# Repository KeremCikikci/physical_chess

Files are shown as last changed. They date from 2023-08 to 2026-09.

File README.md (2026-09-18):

# Physical Chess

https://github.com/KeremCikikci/physical_chess/assets/98697826/390d2253-afeb-4dcd-b02d-cf1ae9b18a00

# Working Principle

The trained artificial intelligence model recognizes the plus-shaped symbols on the game board 
through the camera mounted above the board. The adjacent corners of the symbols define the 
boundaries of the chessboard. As the symbols are detected with an artificial intelligence 
model, the position or angle of the camera can change while still determining the board.

Each frame captured by the camera undergoes various processes to eliminate proportional 
distortions and noise. In the obtained output, each frame is observed individually and 
converted from BGR format to HSV format. 

To reduce errors, colors of chess pieces that are far apart in the spectrum are made more 
distinguishable through different processes. Thus, the colors of the pieces on all squares are 
recorded. Since the positions of the pieces are known at the beginning of a chess game, there 
is no need to determine the types of pieces from the captured image.

For a chess game played on an online platform like Lichess, a unique ID is assigned to the 
game, and necessary information is retrieved using the Lichess API. However, to prevent 
cheating attempts, the Lichess API provides move information with a delay. Therefore, in a 
Lichess game, when a change occurs, a screenshot is taken to detect the move. Moves are 
recorded in the UCI (Universal Chess Interface) notation, which specifies the starting and 
ending coordinates of the pieces.

Additionally, the pieces obtained from Lichess at the beginning of the game are compared with 
the pieces detected in the squares from the camera. If they are not in sync, differing square 
coordinates are marked. When it's a player's turn, data flow is monitored from the Arduino, and 
if the button is pressed, the camera observes the pieces in the squares again. By identifying 
the differing pieces from the previously saved content, it's determined whether any piece has 
been captured. Then, a move notation is created in UCI format, and the move's validity is 
checked. The move is sent to the Lichess game with the assigned ID using the Lichess API. 
Additionally, time information obtained from the API is sent to Arduino via the Serial port.

At the start of each game, motors rotate until switches are triggered, bringing the robot arm 
to its home position. This resets all angle values and motors, enabling the robot arm to move 
to the desired coordinate in subsequent commands. After the home position, the arm moves to a 
waiting position. A function written in the Arduino code determines the slowest and fastest 
motor values on the arm, as well as the instantaneous speed during the motor's duty cycle, 
using a mathematical function.

While power is transmitted via a pulley on the X-axis, reducers are used on the Y and Z axes to 
greatly reduce the motor's speed and increase its torque by about 60 times. These reducers 
allow smooth movement of the load motors without excessive force.

In the final arm segment of the robot, there is a structure that lifts the chess pieces using a 
funnel. When triggered in the center of the funnel, a coil creates a magnetic field to lift the 
pieces by attracting the screws on top of them. Due to the high current drawn by the coil, it's 
triggered by a relay.

In the program, the chessboard is considered a coordinate axis, and after providing the 
coordinates where only the farthest point of the arm will be, the most economical angle values 
for the arm to reach the desired location are calculated. Motors bring the robot to the 
calculated angle values.

The movement path of the arm is determined by the move notation sent from the Serial monitor. 
When the arm movement is complete, it notifies the Python program. Additionally, time 
information is conveyed throughout the game. The remaining time of the opponents is visualised 
on displays. While each LED control of the displays requires 20 separate data wires, with 2 shift 
register chips, the data is transmitted using only 3 wires. The shift registers sequentially 
light up the required LEDs in each segment of the display. This process happens so quickly that 
the human eye perceives the LEDs as lit simultaneously.

# Complete Documentation
[RoboChess_ Digitalisierung auf dem Schachbrett.pdf](https://github.com/user-attachments/files/32381137/RoboChess_.Digitalisierung.auf.dem.Schachbrett.pdf)

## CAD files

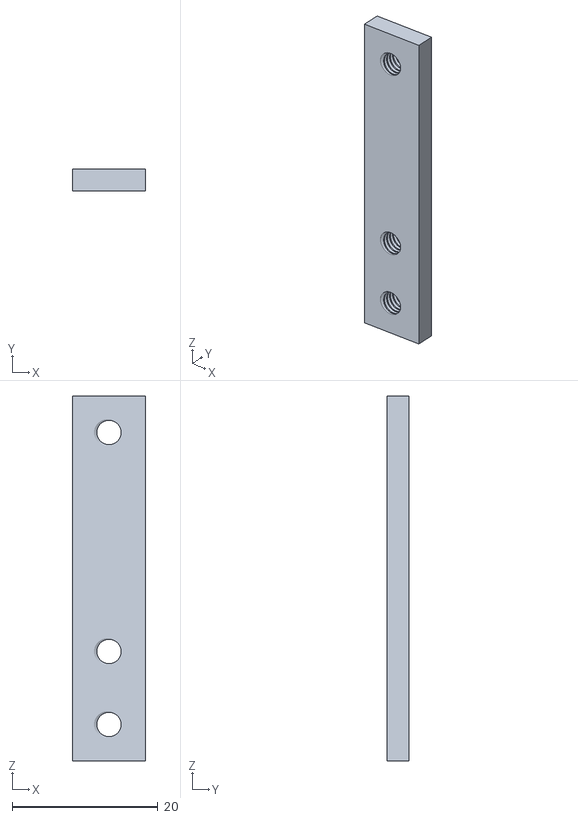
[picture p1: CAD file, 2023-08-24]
3D/cubuk v1.stl
10.0 x 3.00 x 50.0

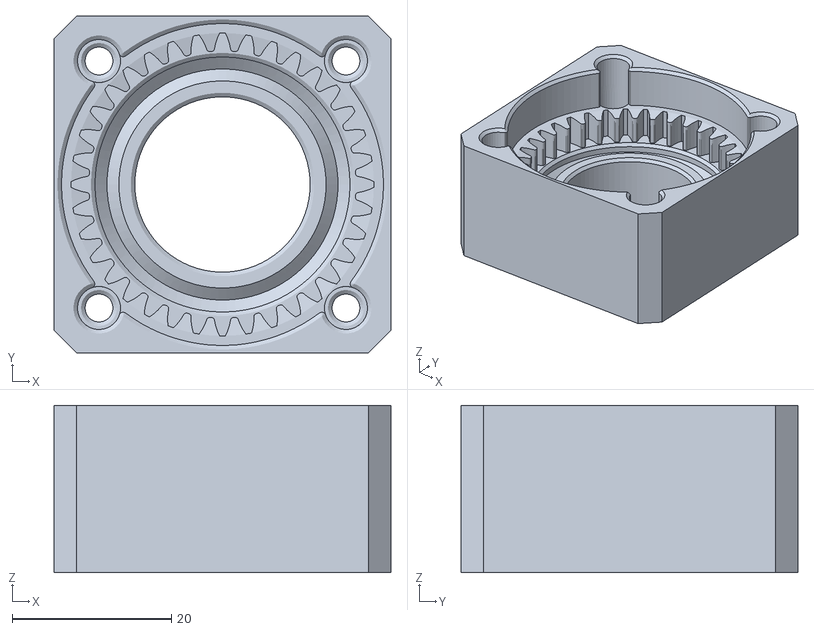
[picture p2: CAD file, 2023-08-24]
3D/redüktör/bpl.stl
42.3 x 42.3 x 21.0

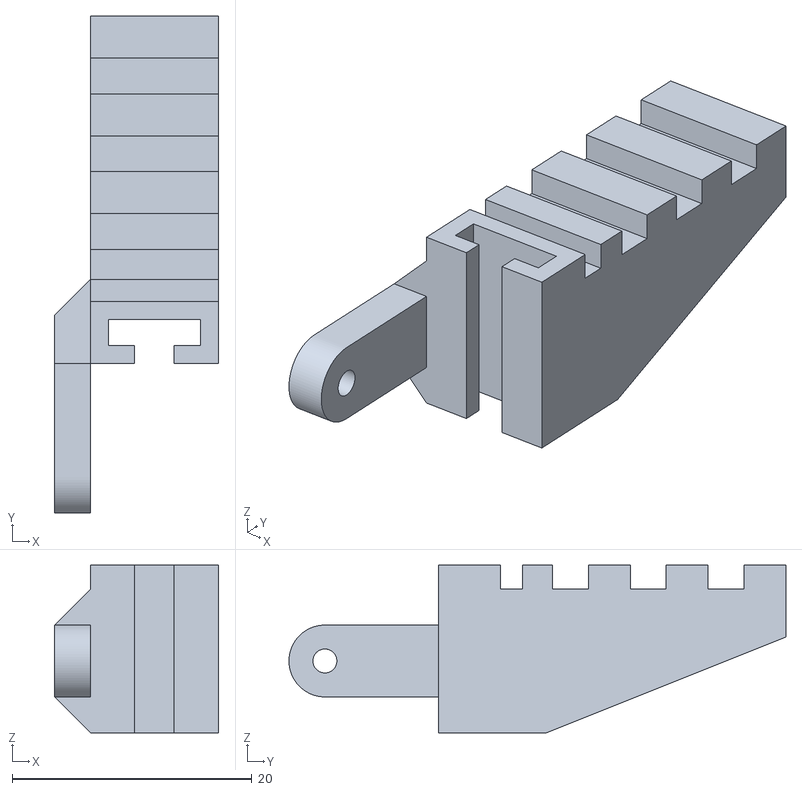
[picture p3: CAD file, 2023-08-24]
3D/tutma/CELUST_1.stl
13.7 x 41.5 x 14.0

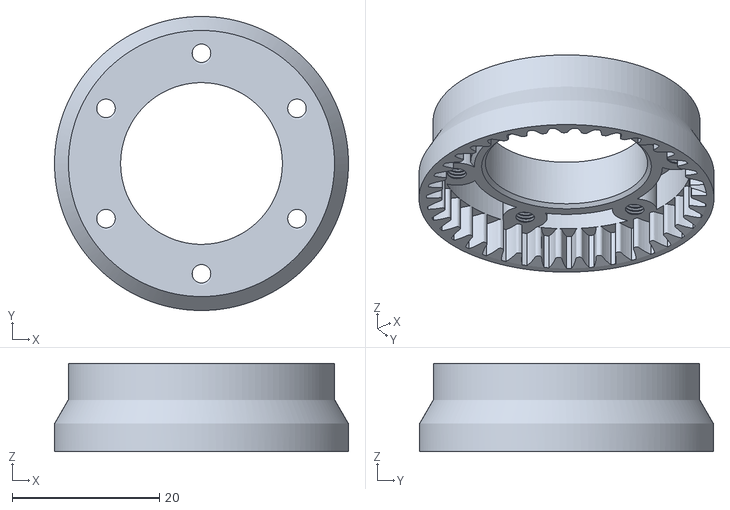
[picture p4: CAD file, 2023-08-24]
3D/redüktör/outring.stl
40.0 x 40.0 x 12.0

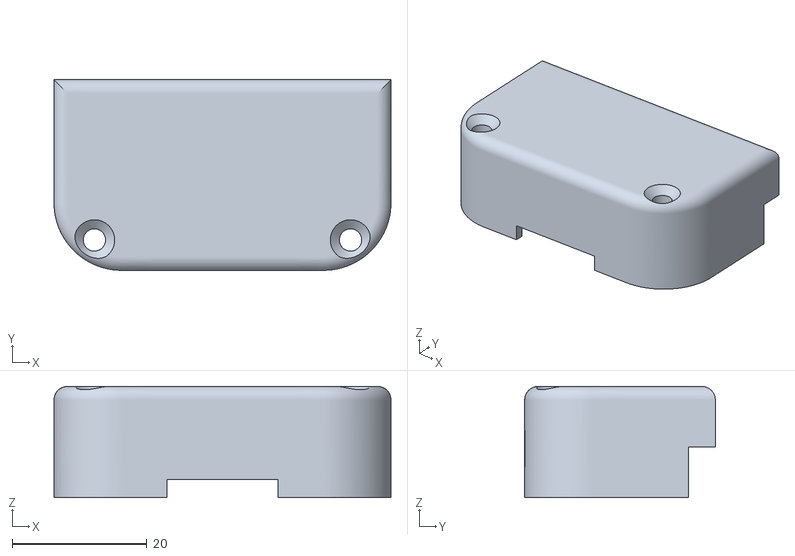
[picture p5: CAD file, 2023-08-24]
3D/tutma/BASE_COVER_2.stl
50.0 x 28.3 x 16.5

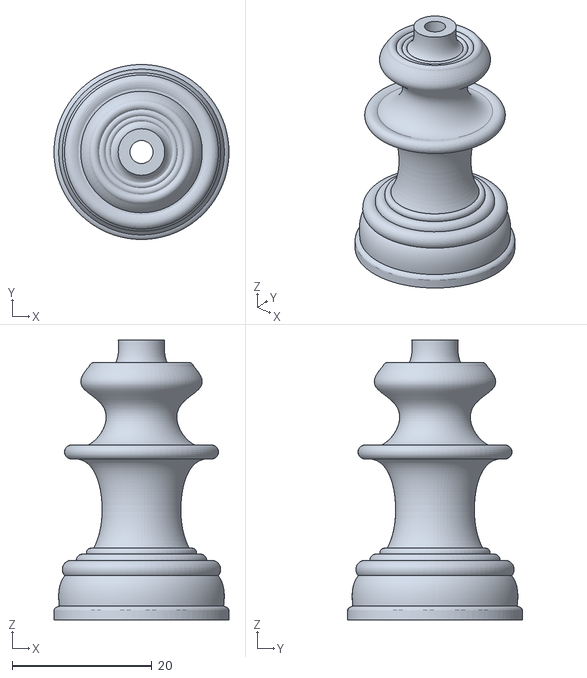
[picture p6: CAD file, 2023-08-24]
3D/vezir v3.stl
25.0 x 25.0 x 40.0

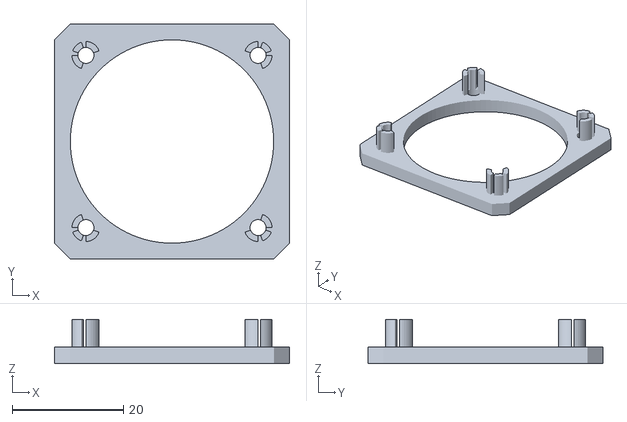
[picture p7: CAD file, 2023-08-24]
3D/redüktör/topcover.stl
42.3 x 42.3 x 8.00

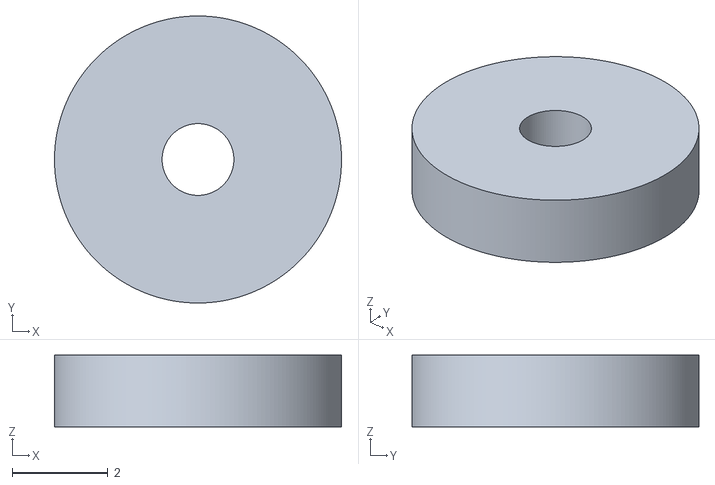
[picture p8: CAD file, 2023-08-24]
3D/tutma/POODLOŽKA.stl
6.00 x 6.00 x 1.50

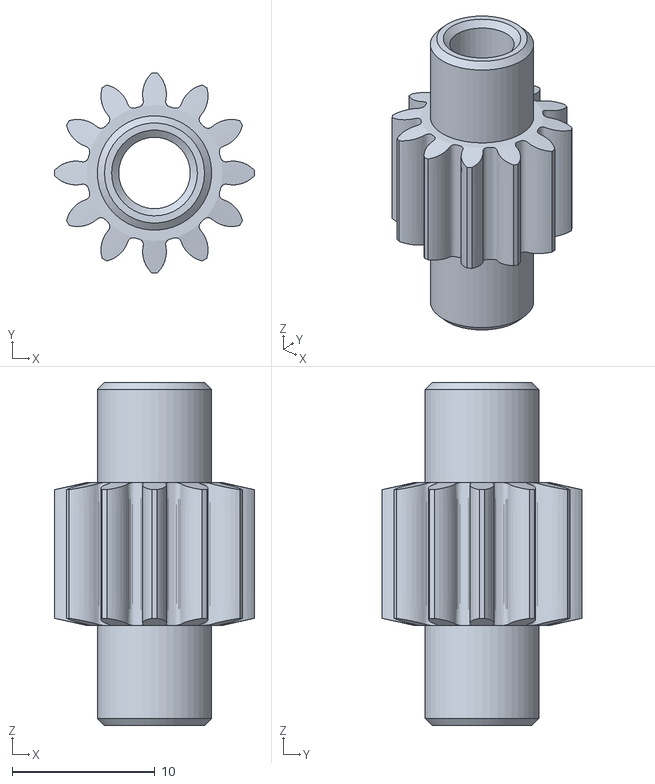
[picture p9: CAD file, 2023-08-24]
3D/redüktör/sun.stl
14.0 x 14.0 x 24.0

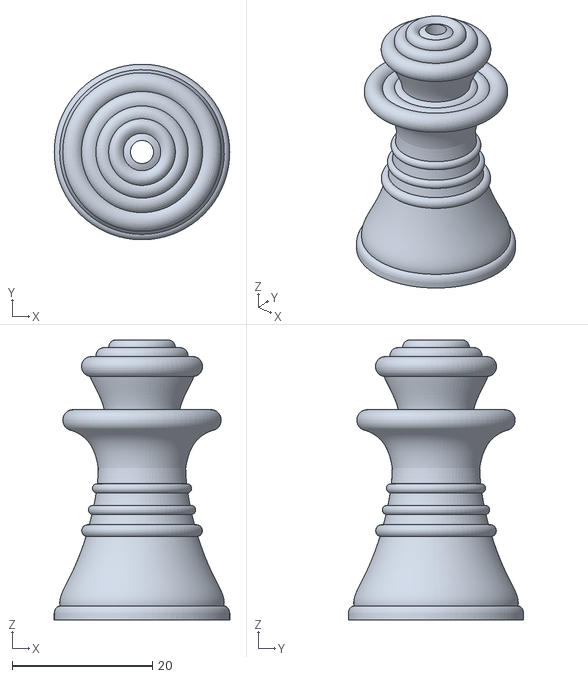
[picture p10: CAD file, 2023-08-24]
3D/sah v1.stl
25.0 x 25.0 x 39.9

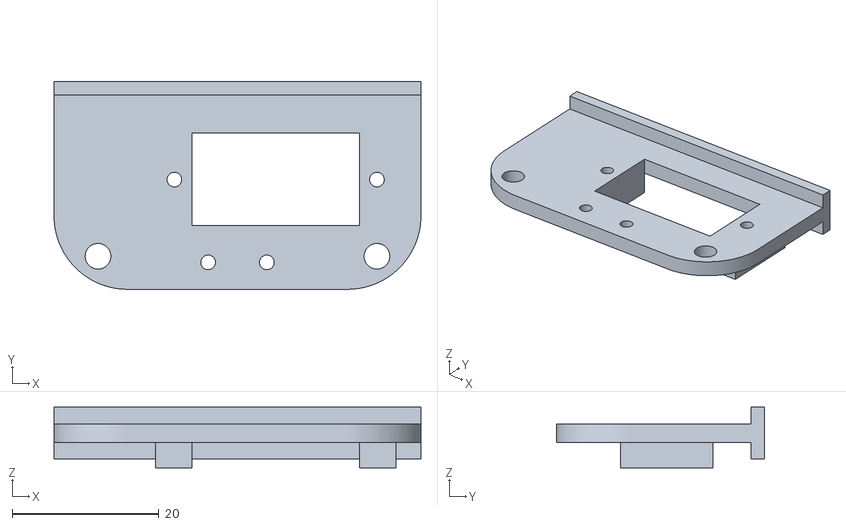
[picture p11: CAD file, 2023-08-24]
3D/tutma/BASE.stl
50.0 x 28.3 x 8.30

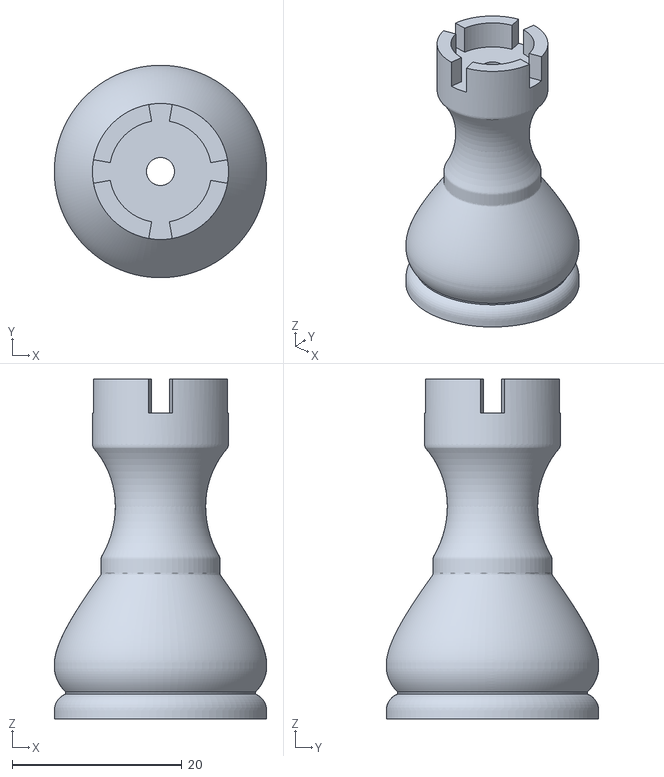
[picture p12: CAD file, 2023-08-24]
3D/kale v3.stl
25.0 x 25.0 x 40.0

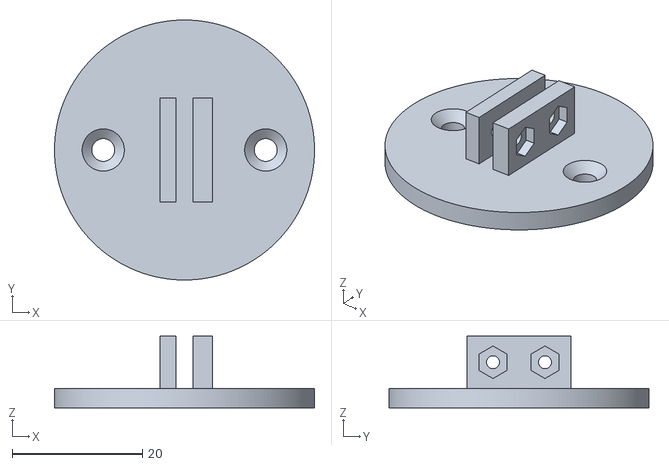
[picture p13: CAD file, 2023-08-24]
3D/tutma/HOUSING.stl
40.0 x 40.0 x 11.0

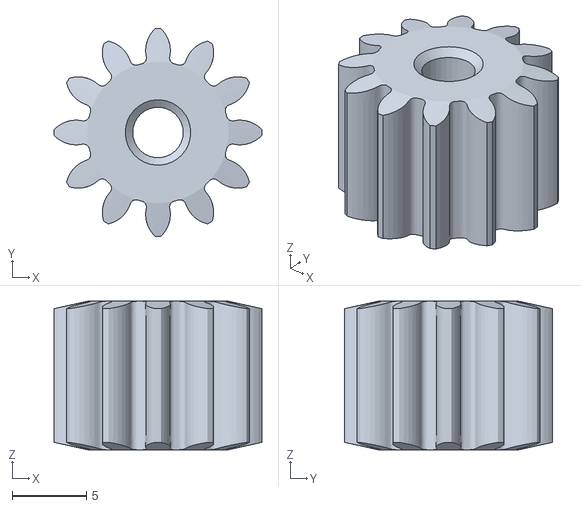
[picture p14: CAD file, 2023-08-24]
3D/redüktör/planet.stl
14.0 x 14.0 x 10.0

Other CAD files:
3D/redüktör/sun v2.stl
3D/tutma/SPOJKA.stl
3D/switchX_holder v3.stl
3D/tutma/CELUST_2.stl
3D/BASE v2.stl
3D/HOUSING v1.stl
3D/Link.stl
3D/at v1.stl
3D/back1 v1.stl
3D/buffer v1.stl
3D/camera_holder v1.stl
3D/cnc2 baski4 v5.f3d
3D/cnc2 baski4 v5.stl
3D/cnc2 baski4 v6.stl
3D/end_lower v1.stl
3D/end_pipe_holder v1.stl
3D/fil v1.stl
3D/fil v2.stl
3D/front1 v1.stl
3D/gripper1 (1) v1.stl
3D/gripper1 (1) v8.stl
3D/gripper2 (1) v1.stl
3D/gripper2 (1) v3.stl
3D/gripper2 (1) v4.stl
3D/gripper3 v1.stl
3D/gripper4 v1.stl
3D/gripperHolder1 v2.stl
3D/gripperHolder2 v1.stl
3D/ground1 v1.stl
3D/huni v0.stl
3D/kale v1.stl
3D/kaplin v1.stl
3D/kaplin v2.stl
3D/knight v1.stl
3D/knight v2.stl
3D/left1 v1.stl
3D/lower v1.stl
3D/mil 10cm v1.stl
3D/mil v1.stl
3D/mil2 v1.stl
3D/mil3 v1.stl
3D/mil_holder v4 v2.stl
3D/nema 17 v1.stl
3D/nema17_holder v4.stl
3D/pion v1.stl
3D/pion_son v1.stl
3D/pion_son v4.stl
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

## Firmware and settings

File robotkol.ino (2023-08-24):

#include <Servo.h>
Servo w;

#define dsP A5
#define latchP A4
#define clockP 13
#define button 11

#define gripper 8

#define dirX  6
#define pulseX 7
#define switchX A3
#define dirY 5
#define pulseY 12
#define switchY A1
#define dirZ  2
#define pulseZ 10
#define switchZ A2

boolean rotX = false; // false: autohome
boolean rotY = true; // false: autohome
boolean rotZ = true; // false: autohome

double SPMX = 10.1;//9.5; // 9.75, 8.5
double SPDY = 28.89;//28.89
double SPDZ = 28.89;

double posX;
double angleA = 0;
double angleB = 0;
double angleC = 90;

int squaresA[8];
int squaresB[8];

int servoBost = 10;

int aAngles_[8][2] = {{110, 87}, {105, 79}, {95, 72}, {85, 64}, {78, 60}, {65, 52}, {57, 46}, {52, 38}};
int bAngles_[8][2] = {{24, 30}, {40, 43}, {55, 55}, {70, 68}, {80, 78}, {90, 90}, {105, 103}, {119, 116}};
int servoBosts[8] = {20, 18, 17, 12, 12, 10, 8, 10};
String alphabet[8] = {"h", "g", "f", "e", "d", "c", "b", "a"};

String move_ = "None";
String capture_ = "None";
String first, second, third, fourth;
int num1, num2;
double squareSize = 40;
double rightPadding = 40;

String data;

unsigned int digits[8] = {32927, 16421, 8205, 4249, 2121, 1089, 539, 257};/*{0, 0, 0, 0, 0, 0, 0, 0};*/

String strBinDig;
String clock_;
String message;

String firstClock;
String secondClock;

boolean turn = true;

unsigned long previousMillis = 0;
const unsigned long interval = 1000;

String segments[10] = {
  "0000001", // 0
  "1001111", // 1
  "0010010", // 2
  "0000110", // 3
  "1001100", // 4
  "0100100", // 5
  "0100000", // 6
  "0001111", // 7
  "0000000", // 8
  "0000100"  // 9
};


void autoHome(int delay_){
  w.write(120);
  rotX = false; // false: autohome
  rotY = false; // false: autohome
  rotZ = false; // false: autohome

  boolean switchXValue;
  boolean switchYValue;
  boolean switchZValue;
  
  digitalWrite(dirX, rotX);
  digitalWrite(dirY, rotY);
  digitalWrite(dirZ, rotZ);

  for(int i = 0; i < (int)(30 * SPDY); i++){
    switchYValue = digitalRead(switchY);
    digitalWrite(pulseY, 1);
    delayMicroseconds(delay_);
    digitalWrite(pulseY, 0);
    delayMicroseconds(delay_);

    if (switchYValue == 1)
      break;
  }
  
  while (true){
    switchXValue = digitalRead(switchX);
    switchYValue = digitalRead(switchY);
    switchZValue = digitalRead(switchZ);
    
    if (switchXValue == 0)
      digitalWrite(pulseX, 1);
      
    if (switchYValue == 0)
      digitalWrite(pulseY, 1);
    
    if (switchZValue == 0)
      digitalWrite(pulseZ, 1);
    
    delayMicroseconds(delay_);
    if (switchXValue == 0)
      digitalWrite(pulseX, 0);
    
    if (switchYValue == 0)
      digitalWrite(pulseY, 0);
    
    if (switchZValue == 0)
      digitalWrite(pulseZ, 0);
    
    if ((switchXValue == 1) && (switchYValue == 1) && (switchZValue == 1)){
      posX = 0;
      angleA = 127.2;//143.3
      angleB = 119;//108
      angleC = 90;

      break;
    }
    delayMicroseconds(delay_);
  }
  w.write(90);
}

int findMax(int a, int b, int c) {
  int maxVal = a;

  if (b > maxVal) {
    maxVal = b;
  }

  if (c > maxVal) {
    maxVal = c;
  }

  return maxVal;
}

void goPos(double xPosToGo, double aAngleToGo, double bAngleToGo, int minSpeed, int maxSpeed, int servoBost = 0){
  double deltaPosX = posX - xPosToGo;
  double deltaAngleA = angleA - aAngleToGo;
  double deltaAngleB = angleB - bAngleToGo;
  
  double posX_ = posX;
  double angleA_ = angleA;
  double angleB_ = angleB;
  
  int stepsX = abs(deltaPosX * SPMX);
  int stepsA = abs(deltaAngleA * SPDY);
  int stepsB = abs(deltaAngleB * SPDZ);

  int maxStep = findMax(stepsX, stepsA, stepsB);
  
  int steppedX = 0;
  int steppedA = 0;
  int steppedB = 0;
  
  double steppedAngleA = 0;
  double steppedAngleB = 0;

  rotX = true;
  rotY = false;
  rotZ = false;

  if (deltaPosX > 0)
    rotX = false;
  if (deltaAngleA > 0)
    rotY = true;
  if (deltaAngleB > 0)
    rotZ = true;

  digitalWrite(dirX, rotX);
  digitalWrite(dirY, rotY);
  digitalWrite(dirZ, rotZ);
    
  int phrase = 1;
  
  int lengthOfPhrase1 = maxStep/3;
  int lengthOfPhrase3 = maxStep/3;
  
  int delay_;

  int counter = 0;
  
  while (true){
    unsigned long currentMillis = millis();
    
    boolean switchXValue = digitalRead(switchX);
    boolean switchYValue = digitalRead(switchY);
    boolean switchZValue = digitalRead(switchZ);
/*
    if (((switchXValue == 1) || (switchYValue == 1) || (switchZValue == 1)) && (counter > 2000)){
      autoHome(500);
      break;
    }*/

    if (currentMillis - previousMillis >= interval) {
    previousMillis = currentMillis;

    if (turn == false){
      firstClock = String(firstClock.toInt()-1);
      int zeros = 4 - firstClock.length();
      for (int i = 0; i < zeros; i++){
        firstClock = "0" + firstClock;
      }
    }
    else{
      secondClock = String(secondClock.toInt()-1);
      int zeros = 4 - secondClock.length();
      for (int i = 0; i < zeros; i++){
        secondClock = "0" + secondClock;
      }
    }
    clock_ = formatTime(firstClock.toInt()) + formatTime(secondClock.toInt());
    formatClock();
  }
  
    counter++;
    
    stepsX--;
    stepsA--;
    stepsB--;

    if ((steppedX > maxStep - lengthOfPhrase3) || (steppedA > maxStep - lengthOfPhrase3) || (steppedB > maxStep - lengthOfPhrase3))
      phrase = 3;
    else if ((steppedX > lengthOfPhrase1) || (steppedA > lengthOfPhrase1) || (steppedB > lengthOfPhrase1))
      phrase = 2;

    if (phrase == 3)
      delay_ = map(counter, maxStep - lengthOfPhrase3, maxStep, maxSpeed, minSpeed);
    if (phrase == 2)
      delay_ = maxSpeed;
    if (phrase == 1)
      delay_ = map(counter, 0, lengthOfPhrase1, minSpeed, maxSpeed);
    
    if (stepsX >= 0){
      digitalWrite(pulseX, 1); 
    }
       
    if (stepsA >= 0){
      digitalWrite(pulseY, 1);
    }
      
    if (stepsB >= 0){
      digitalWrite(pulseZ, 1);
    }
      
    delayMicroseconds(delay_);

    if (stepsX >= 0){
      digitalWrite(pulseX, 0);
      steppedX++;
    }
    if (stepsA >= 0){
      digitalWrite(pulseY, 0);
      steppedA++;
    }
    if (stepsB >= 0){
      digitalWrite(pulseZ, 0);
      steppedB++;
    }
    
    if ((stepsX < 0) && (stepsA < 0) && (stepsB < 0)){
      posX = xPosToGo;
      angleA = aAngleToGo;
      angleB = bAngleToGo;
      
      break;
    }

    steppedAngleA = steppedA / SPDY;
    steppedAngleB = steppedB / SPDZ;

    if (rotX == false)
      posX = posX + steppedX;
    else
      posX = posX - steppedX;
      
    if (rotY == false)
      angleA = angleA_ + steppedAngleA;
    else
      angleA = angleA_ - steppedAngleA;

    if (rotZ == false)
      angleB = angleB_ + steppedAngleB;
    else
      angleB = angleB_ - steppedAngleB;

    angleC = 270 - angleA - angleB;

    if ((angleC > 60) && (angleC < 160))
      w.write(angleC + servoBost);
      //Serial.println(angleC);
    delayMicroseconds(delay_);
  }
  posX = xPosToGo;
  angleA = aAngleToGo;
  angleB = bAngleToGo;
}

int findIndexOfChar(String str, String target) {
  int strLength = str.length();
  int targetLength = target.length();
  
  for (int i = 0; i <= strLength - targetLength; i++) {
    if (str.substring(i, i + targetLength) == target) {
      return i; // Eğer hedef string bulunursa indeksi döndür
    }
  }
  
  return -1;
}
int findIndexOfStringInList(String list[], String targetString) {
  for (int i = 0; i < 8; i++) {
    if (list[i] == targetString) {
      return i; // String karakterini içeren stringin indeksini döndür
    }
  }
  return -1; // String karakterini içeren string bulunamazsa -1 döndür
}
void formatClock(){
  for (int i = 0; i < clock_.length(); i++) {
        // pre 0 s
        for (int pre0s = 0; pre0s < i; pre0s++){
          strBinDig.concat("0");
        }
        // 1
        strBinDig.concat("1");
        // post 0 s
        for (int post0s = 0; post0s < clock_.length() - i - 1; post0s++){
          strBinDig.concat("0");
        }
        strBinDig.concat(segments[clock_.charAt(i) - '0']);
        // point
        if ((i == 1) || (i == 5)){
          strBinDig.concat("0");
        }
        else{
          strBinDig.concat("1");
        }
        long decDig = strtol(strBinDig.c_str(), NULL, 2);
        digits[i] = decDig;
        strBinDig = "";
      }
}

String formatTime(unsigned int totalSeconds) {
  unsigned int minutes = totalSeconds / 60;
  unsigned int seconds = totalSeconds % 60;

  String formattedTime = "";

  if (minutes < 10) {
    formattedTime += "0";
  }
  formattedTime += String(minutes);

  if (seconds < 10) {
    formattedTime += "0";
  }
  formattedTime += String(seconds);

  return formattedTime;
}

void setup(){
  pinMode(dsP, OUTPUT);
  pinMode(latchP, OUTPUT);
  pinMode(clockP, OUTPUT);
  pinMode(button, INPUT);
  
  pinMode(dirX, OUTPUT);
  pinMode(pulseX, OUTPUT);
  pinMode(switchX, INPUT);
  pinMode(dirY, OUTPUT);
  pinMode(pulseY, OUTPUT);
  pinMode(switchY, INPUT);
  pinMode(dirZ, OUTPUT);
  pinMode(pulseZ, OUTPUT);
  pinMode(switchZ, INPUT);
  pinMode(gripper, OUTPUT);
  w.attach(9);
  digitalWrite(gripper, 0);

  Serial.begin(115200);
  Serial.setTimeout(1);
  digitalWrite(dirX, rotX);
  digitalWrite(dirY, rotY);
  digitalWrite(dirZ, rotZ);/*
  for(int i = 0; i < (int)(SPDY * 100); i++){
    digitalWrite(dirY, 1);
    digitalWrite(pulseY, 1);
    delayMicroseconds(500);
    digitalWrite(pulseY, 0);
    delayMicroseconds(500);
  }*/
/*
  for(int i = 0; i < (int)(SPDZ * 360); i++){
    digitalWrite(dirZ, 1);
    digitalWrite(pulseZ, 1);
    delayMicroseconds(500);
    digitalWrite(pulseZ, 0);
    delayMicroseconds(500);
  }*/
  autoHome(500);
  digitalWrite(gripper,0);
  goPos(0, 90, 90, 1000, 400, 0);
}


void loop(){
  unsigned long currentMillis = millis();
  
  if (digitalRead(button) == 0)
      Serial.println("move");
      
  if (Serial.available() > 0){
    delay(100);
    if (Serial.available() > 0){
      data =  Serial.readStringUntil('\n');
      Serial.println("O");
      // clock
      if (data.length() == 8){
        if (turn == true)
          turn = false;
        else
          turn = true;
        
        firstClock = data.substring(0, 4);
        secondClock = data.substring(4);
        clock_ = formatTime(firstClock.toInt()) + formatTime(secondClock.toInt());
        Serial.println(clock_);
        formatClock();
      }
      // hamleyi gönder
      // castles
      else if (data == "S"){
        // ilk kare 
        digitalWrite(gripper, 0);
        goPos(20 + rightPadding, aAngles_[0][0], bAngles_[0][0], 1000, 400, servoBosts[0]);
        digitalWrite(gripper, 1);
        delay(250);
        goPos(20 + rightPadding, aAngles_[0][1], bAngles_[0][1], 1800, 1200, servoBosts[0]);
        delay(250);
        goPos(20 + rightPadding, aAngles_[0][0], bAngles_[0][0], 1800, 1200, servoBosts[0]);
        delay(250);
        
        // ucuncu kare
        goPos(100 + rightPadding, aAngles_[0][0], bAngles_[0][0], 1000, 400, servoBosts[0]);
        delay(250);
        goPos(100 + rightPadding, aAngles_[0][1], bAngles_[0][1], 1800, 1200, servoBosts[0]);
        digitalWrite(gripper, 0);
        delay(250);
        goPos(100 + rightPadding, aAngles_[0][0], bAngles_[0][0], 1800, 1200, servoBosts[0]);
        delay(250);

        // dördüncü kare
        goPos(140 + rightPadding, aAngles_[0][0], bAngles_[0][0], 1000, 400, servoBosts[0]);
        digitalWrite(gripper, 1);
        delay(250);
        goPos(140 + rightPadding, aAngles_[0][1], bAngles_[0][1], 1800, 1200, servoBosts[0]);
        delay(250);
        goPos(140 + rightPadding, aAngles_[0][0], bAngles_[0][0], 1800, 1200, servoBosts[0]);
        delay(250);
        
        // ikinci kare
        goPos(60 + rightPadding, aAngles_[0][0], bAngles_[0][0], 1000, 400, servoBosts[0]);
        delay(250);
        goPos(60 + rightPadding, aAngles_[0][1], bAngles_[0][1], 1800, 1200, servoBosts[0]);
        digitalWrite(gripper, 0);
        delay(250);
        goPos(60 + rightPadding, aAngles_[0][0], bAngles_[0][0], 1800, 1200, servoBosts[0]);
        delay(250);

        goPos(0, 90, 90, 1000, 400, 0);
      }

      else if (data == "L"){
        // 4. kare 
        digitalWrite(gripper, 0);
        goPos(140 + rightPadding, aAngles_[0][0], bAngles_[0][0], 1000, 400, servoBosts[0]);
        digitalWrite(gripper, 1);
        delay(250);
        goPos(140 + rightPadding, aAngles_[0][1], bAngles_[0][1], 1800, 1200, servoBosts[0]);
        delay(250);
        goPos(140 + rightPadding, aAngles_[0][0], bAngles_[0][0], 1800, 1200, servoBosts[0]);
        delay(250);
        
        // 6. kare
        goPos(220 + rightPadding, aAngles_[0][0], bAngles_[0][0], 1000, 400, servoBosts[0]);
        delay(250);
        goPos(220 + rightPadding, aAngles_[0][1], bAngles_[0][1], 1800, 1200, servoBosts[0]);
        digitalWrite(gripper, 0);
        delay(250);
        goPos(220 + rightPadding, aAngles_[0][0], bAngles_[0][0], 1800, 1200, servoBosts[0]);
        delay(250);

        // 8. kare
        goPos(300 + rightPadding, aAngles_[0][0], bAngles_[0][0], 1000, 400, servoBosts[0]);
        digitalWrite(gripper, 1);
        delay(250);
        goPos(300 + rightPadding, aAngles_[0][1], bAngles_[0][1], 1800, 1200, servoBosts[0]);
        delay(250);
        goPos(300 + rightPadding, aAngles_[0][0], bAngles_[0][0], 1800, 1200, servoBosts[0]);
        delay(250);
        
        // 5. kare
        goPos(180 + rightPadding, aAngles_[0][0], bAngles_[0][0], 1000, 400, servoBosts[0]);
        delay(250);
        goPos(180 + rightPadding, aAngles_[0][1], bAngles_[0][1], 1800, 1200, servoBosts[0]);
        digitalWrite(gripper, 0);
        delay(250);
        goPos(180 + rightPadding, aAngles_[0][0], bAngles_[0][0], 1800, 1200, servoBosts[0]);
        delay(250);

        goPos(0, 90, 90, 1000, 400, 0);
      }
      
      else if (((data == "M") && (move_ != "None")) || ((data == "C") && (move_ != "None"))){
        num1 = second.toInt() - 1;
        num2 = fourth.toInt() - 1;

        // 1. Yukarda
        double x1 = findIndexOfStringInList(alphabet, first) * squareSize + squareSize / 2 + rightPadding;
        int y1 = num1;
        double a1Y = aAngles_[y1][0];
        double b1Y = bAngles_[y1][0];

        // 1. Assada
        double a1A = aAngles_[y1][1];
        double b1A = bAngles_[y1][1];

        // 2. Yukarda
        double x2 = findIndexOfStringInList(alphabet, third) * squareSize + squareSize / 2 + rightPadding;
        int y2 = num2;
        double a2Y = aAngles_[y2][0];
        double b2Y = bAngles_[y2][0];

        // 2. Assada
        double a2A = aAngles_[y2][1];
        double b2A = bAngles_[y2][1];
        
        // Harakete gec
        // tas yenirse
        if (data == "C"){
          // 2. Tasin üstüne git
          digitalWrite(gripper, 0);
          goPos(x2, a2Y, b2Y, 1000, 400, servoBosts[y2 ]);
          delay(250);
          digitalWrite(gripper, 1);

          // 2. i al
          goPos(x2, a2A, b2A, 1800, 1200, servoBosts[y2 ]);
          delay(250);
          goPos(x2, a2Y, b2Y, 1800, 1200, servoBosts[y2 ]);
          delay(250);

          // kenara at
          goPos(0, 65, 90, 1000, 400, 0);
          delay(250);
          digitalWrite(gripper, 0);
        }
        
        // 1. Tasin üstüne git
        digitalWrite(gripper, 0);
        delay(250);
        goPos(x1, a1Y, b1Y, 1000, 400, servoBosts[y1 ]);
        delay(250);

        // 1. Tasi al
        digitalWrite(gripper, 1);
        delay(250);
        goPos(x1, a1A, b1A, 1800, 1000, servoBosts[y1 ]);
        delay(250);
        goPos(x1, a1Y, b1Y, 1800, 1000, servoBosts[y1 ]);
        delay(250);

        // 2. Tasin üstüne git
        goPos(x1 - (x1 - x2)/2, a2Y+10, b2Y-5, 1000, 400, servoBosts[y2 ]);
        goPos(x2, a2Y, b2Y, 1000, 400, servoBosts[y2 ]);
        delay(250);
        
        // 2. Tasi birak;
        goPos(x2, a2A, b2A, 1800, 1000, servoBosts[y2 ]);
        delay(250);
        digitalWrite(gripper, 0);
        delay(1000);
        goPos(x2, a2Y+2, b2Y+1, 1800, 1000, servoBosts[y2 ]);
        delay(250);
        goPos(0, 90, 90, 600, 400, 0);
        delay(250);
        
        
        move_ = "None";
      }
      
      // hamleyi cek
      else if (data.length() == 4){
        move_ = data;

        first = move_.substring(0, 1);
        second = move_.substring(1, 2);
        third = move_.substring(2, 3);
        fourth = move_.substring(3, 4);
      }
    }
  }
  for (int i = 0; i < 8; i++){
    byte lowLED  = lowByte(digits[i]);
    byte highLED = highByte(digits[i]);
    
    digitalWrite(latchP, 0);
    
    shiftOut(dsP, clockP, LSBFIRST, lowLED);
    shiftOut(dsP, clockP, LSBFIRST, highLED);
    
    digitalWrite(latchP, 1);
    delay(2);
  }
  if (currentMillis - previousMillis >= interval) {
    previousMillis = currentMillis;

    if (turn == false){
      firstClock = String(firstClock.toInt()-1);
      int zeros = 4 - firstClock.length();
      for (int i = 0; i < zeros; i++){
        firstClock = "0" + firstClock;
      }
    }
    else{
      secondClock = String(secondClock.toInt()-1);
      int zeros = 4 - secondClock.length();
      for (int i = 0; i < zeros; i++){
        secondClock = "0" + secondClock;
      }
    }
    clock_ = formatTime(firstClock.toInt()) + formatTime(secondClock.toInt());
    formatClock();
  }
}

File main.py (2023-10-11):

import cv2
from ultralytics import YOLO
import numpy as np

from datetime import timedelta, datetime
import serial
import copy
import time

import berserk
from PIL import ImageGrab
from colorama import init, Fore, Style

init(autoreset=True)

SYMDETECTION = False
SELECTBOARD = False

gameID = 'Gr1QuKkK'

width = 1280
height = 720

if SYMDETECTION:
    model = YOLO('weights/best.pt')

contents = [["BLACK", "BLACK", "SPACE", "SPACE", "SPACE", "SPACE", "WHITE", "WHITE"],
            ["BLACK", "BLACK", "SPACE", "SPACE", "SPACE", "SPACE", "WHITE", "WHITE"],
            ["BLACK", "BLACK", "SPACE", "SPACE", "SPACE", "SPACE", "WHITE", "WHITE"],
            ["BLACK", "BLACK", "SPACE", "SPACE", "SPACE", "SPACE", "WHITE", "WHITE"],
            ["BLACK", "BLACK", "SPACE", "SPACE", "SPACE", "SPACE", "WHITE", "WHITE"],
            ["BLACK", "BLACK", "SPACE", "SPACE", "SPACE", "SPACE", "WHITE", "WHITE"],
            ["BLACK", "BLACK", "SPACE", "SPACE", "SPACE", "SPACE", "WHITE", "WHITE"],
            ["BLACK", "BLACK", "SPACE", "SPACE", "SPACE", "SPACE", "WHITE", "WHITE"]]

liContents = copy.deepcopy(contents)

alphabet = ['a', 'b', 'c', 'd', 'e', 'f', 'g', 'h']

color_threshold = .12
color_threshold_lichess = .1

lowerBlue_hsv = (100, 115, 70) # (100, 120, 50)
upperBlue_hsv = (130, 185, 255)# (130, 185, 255)
lowerRed_hsv = (150, 120, 60) # (0, 10, 0)
upperRed_hsv = (250, 195, 250)

lowerWhite_hsv = (0, 0, 50)#(80, 60, 50)#cv2.cvtColor(np.uint8([[lowerOr]]), cv2.COLOR_BGR2HSV)
upperWhite_hsv = (5, 3, 255)#(130, 185, 255)
lowerBlack_hsv = (0, 0, 0)# (0, 10, 0)
upperBlack_hsv = (5, 3, 50)

x1, y1, x2, y2 = 400, 160, 905, 670

fx = 914.413655169
fy = 915.827825362
cx = 634.088633608
cy = 373.530293726
k1 = -0.474162217
k2 = 0.296860407
k3 = 0.000851414
k4 = -0.001612337

rightPadding = 34 # [mm]

squareSize = 40 # [mm]

API_TOKEN = 'lip_I07d8jqSPHAYzacfCumR'
session = berserk.TokenSession(API_TOKEN)
client = berserk.Client(session=session)

arduino = serial.Serial(port='COM3', baudrate=115200, timeout=0)

button_trigger = datetime.now()
getMove_trigger = datetime.now()
clock_trigger = datetime.now()

turn = "BLACK"

def makeTheMove(move, captured):
    # clock
    clocks = client.games.export(gameID)["clocks"]

    whiteClock = None
    blackClock = None

    if len(clocks) >= 2:
        if len(clocks) % 2 == 0:
            whiteClock = clocks[-2] // 100
            blackClock = clocks[-1] // 100
        else:
            whiteClock = clocks[-1] // 100
            blackClock = clocks[-2] // 100

        clock = str(whiteClock) + str(blackClock)
        arduino.write(bytes(clock, 'utf-8'))
    time.sleep(.2)

    arduino.write(bytes(move, 'utf-8'))
    time.sleep(.2)
    
    if move != "SHOR" or move != "LONG":
        if captured:
            arduino.write(bytes("C", 'utf-8'))
        else:
            arduino.write(bytes("M", 'utf-8'))

    else:
        arduino.write(bytes(move[0], 'utf-8'))


def fisheye_correction(img, fx, fy, cx, cy, k1, k2, k3, k4):
    K = np.array([[fx, 0, cx],
                  [0, fy, cy],
                  [0, 0, 1]], dtype=np.float64)

    D = np.array([k1, k2, k3, k4], dtype=np.float64)
    
    corrected_img = cv2.fisheye.undistortImage(img, K, D, Knew=K)
    return corrected_img

def getContent(board, EXAMPLE = False):
    for x in range(8):
        for y in range(8):
            square = board[topLeftCorner[1] + squareHEIGHT * y:topLeftCorner[1] + squareHEIGHT * (y+1), topLeftCorner[0] + squareWIDTH * x:topLeftCorner[0] + squareWIDTH * (x+1)]
            square = cv2.cvtColor(square, cv2.COLOR_BGR2HSV)

            if EXAMPLE:
                cv2.imwrite('assets/' + alphabet[x] + str(8-y) + ".jpg", square)

            mask_black = cv2.inRange(square, lowerBlue_hsv, upperBlue_hsv)
            mask_white = cv2.inRange(square, lowerRed_hsv, upperRed_hsv)

            # Mavi icin
            black_pixels = np.sum(mask_black > 0)
            black_intensity = black_pixels / square_pixels

            # Kirmizi icin
            white_pixels = np.sum(mask_white > 0)
            white_intensity = white_pixels / square_pixels
            
            content = "SPACE"

            if white_intensity > color_threshold or black_intensity > color_threshold:
                if black_intensity >= white_intensity:
                    content = "BLACK"
                else:
                    content = "WHITE"

            contents[x][7 - y] = content

    return contents

def getLiContent():
    ss = ImageGrab.grab(bbox=(x1, y1, x2, y2))
    
    width, height = ss.size
    total_pixels = width * height / 64
    squareWidth, squareHeight = width // 8, height // 8
    ss.save("s.jpg")
    for h in range(0, 8):
        for n in range(0, 8):
            square = (h * squareWidth, n * squareHeight, (h+1)*squareWidth, (n+1)*squareHeight)
            cropped = np.array(ss.crop(square))
            cropped = cv2.cvtColor(cropped, cv2.COLOR_BGR2HSV)

            mask_white = cv2.inRange(cropped, lowerWhite_hsv, upperWhite_hsv)
            mask_black = cv2.inRange(cropped, lowerBlack_hsv, upperBlack_hsv)

            white_pixels = np.sum(mask_white > 0)
            white_intensity = white_pixels / total_pixels

            black_pixels = np.sum(mask_black > 0)
            black_intensity = black_pixels / total_pixels
            c = "SPACE"

            if white_intensity > color_threshold_lichess or black_intensity > color_threshold_lichess:
                if white_intensity >= black_intensity:
                    c = "WHITE"
                else:
                    c = "BLACK"
            
            #liContents[h][n] = c
            
            # Horizontal Reverse Version
            liContents[7- h][n] = c 
    
    return liContents

def getChanges(list1, list2):
    changes = []
    for i in range(len(list1)):
        for a in range(len(list1[0])):
            if list1[i][a] != list2[i][a]:
                changes.append(alphabet[i] + str(a + 1))
    
    return changes

def getMove(changes, preContents, turn):
    captured = None

    # Rok durumu
    if len(changes) == 4:
        if all(element in changes for element in ['e1', 'f1', 'g1', 'h1']) or all(element in changes for element in ['e8', 'f8', 'g8', 'h8']):
            return "SHOR", captured
        else:
            return "LONG", captured
    
    if len(changes) == 2:
        from_ = None
        to_ = None

        for change in changes:
            letter = alphabet.index(change[0])
            number = int(change[-1]) - 1
            
            if preContents[letter][number] == "SPACE":
                from_ = change
            else:
                to_ = change
        
        letter = alphabet.index(to_[0])
        number = int(to_[1]) - 1
        if contents[letter][number] != "SPACE":
            captured = to_
            
        return from_ + to_, captured
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
